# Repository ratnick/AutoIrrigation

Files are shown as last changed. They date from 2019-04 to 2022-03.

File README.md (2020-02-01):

*AUTONOMOUS CLOUD BASED IRRIGATION SYSTEM*

Pitch
=====

Autonomous watering system based on Arduino WEMOS D1 mini, controlled via
Android app through Firebase cloud. PCB design. Case designed and 3D printed.
Key features: Wifi multi-hotspot, Timed Deep sleep / wake-up, persistent memory
in sync with cloud, multiplexing of analogue inputs, Secure Cloud communication.
Updated to also support an MQ-7 CO monitor (https://www.instructables.com/id/Arduino-CO-Monitor-Using-MQ-7-Sensor/).

Table of contents
=================

[1 Pitch 1](#_Toc28007739)

[2 Table of contents 1](#table-of-contents)

[3 Purpose & Description 1](#purpose-description)

[4 Overall Design drivers 1](#overall-design-drivers)

[5 What you will need to get going…and done.
1](#what-you-will-need-to-get-goingand-done.)

[6 System overview 1](#system-overview)

[7 Hardware & PCB 1](#hardware-pcb)

[8 Data flow & global data structure 1](#data-flow-global-data-structure)

[9 Google Firebase Cloud 1](#google-firebase-cloud)

[10 Arduino control software 1](#arduino-control-software)

[11 Android App 1](#android-app)

[12 Cross-platform: Adding new fields in database
1](#cross-platform-adding-new-fields-in-database)

[13 3D printed case 1](#d-printed-case)

[14 Physical Water supply 1](#physical-water-supply)

[15 Connecting it all 1](#connecting-it-all)

[16 Daily use, installation, tuning 1](#daily-use-installation-tuning)

[17 Appendix A - Hardware & PCB version 6.0 - not tested
1](#appendix-a---hardware-pcb-version-6.0---not-tested)

[18 Log History 1](#log-history)

Purpose & Description
=====================

Key use case: I wanted to have an autonomous watering system for outdoor
watering on a city terrasse with the following main requirements:

-   Easy installation:

    -   No wires or cabling

    -   A low-pressure thin water tube to each water station

-   Easy use

    -   No maintenance or battery exchange

    -   Monitoring and control from app

    -   Can run autonomously for at least 3 weeks (during a holiday)

-   Easy scale

    -   Low price per unit

    -   Easy assembly

    -   Reproducible

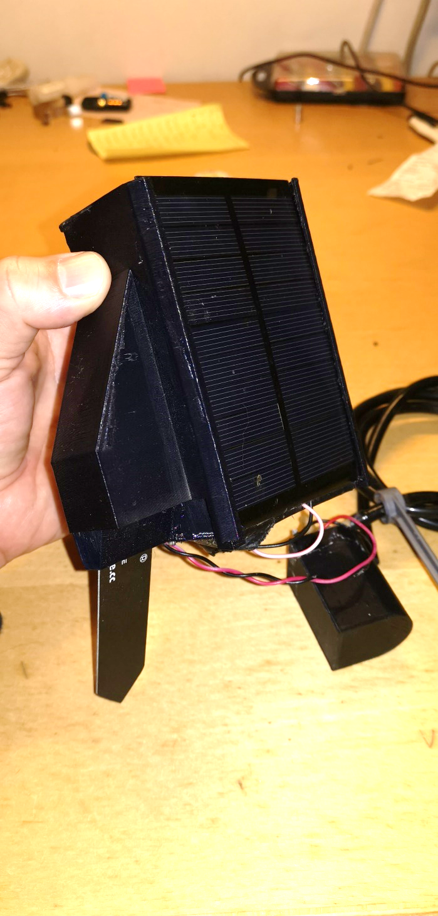
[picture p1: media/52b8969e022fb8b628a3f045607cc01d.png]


Figur 1. The finished unit. Ready to plug into the soil.

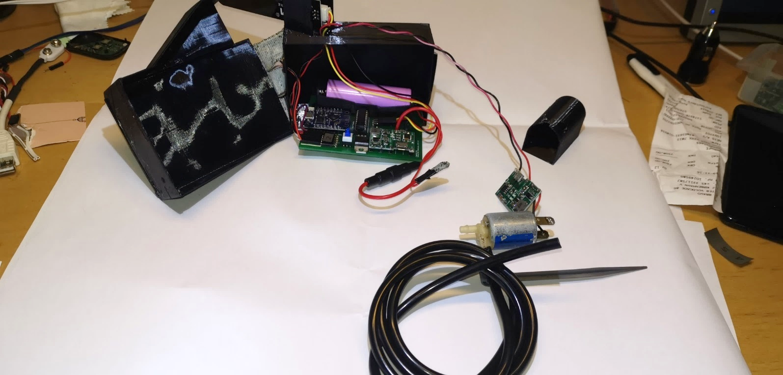
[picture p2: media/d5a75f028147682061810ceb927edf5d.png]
A close up of a piece of paper Description automatically generated


Figur . Same unit - disassembled

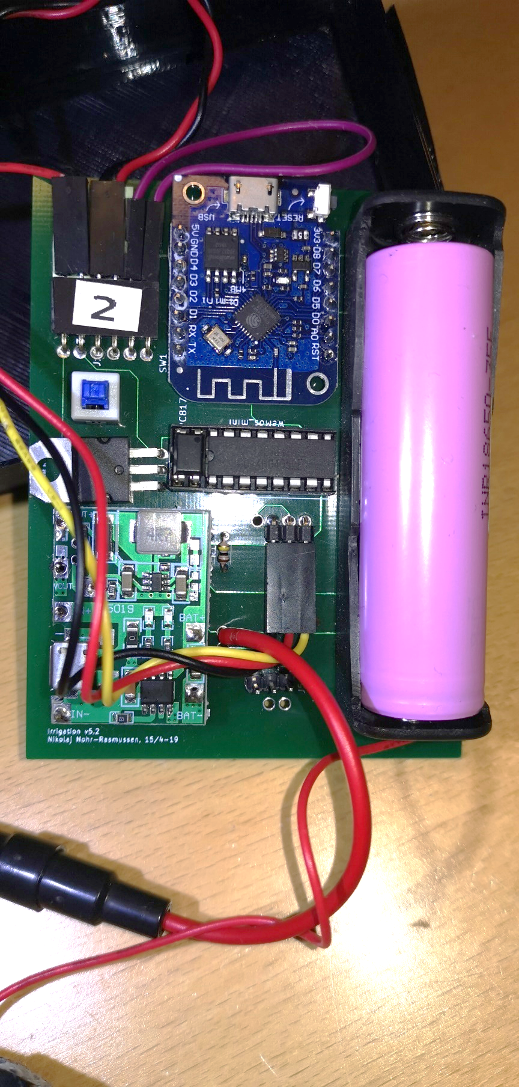
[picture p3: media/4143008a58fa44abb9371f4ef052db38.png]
A circuit board Description automatically generated


Figur 3. Close-up of the PCB

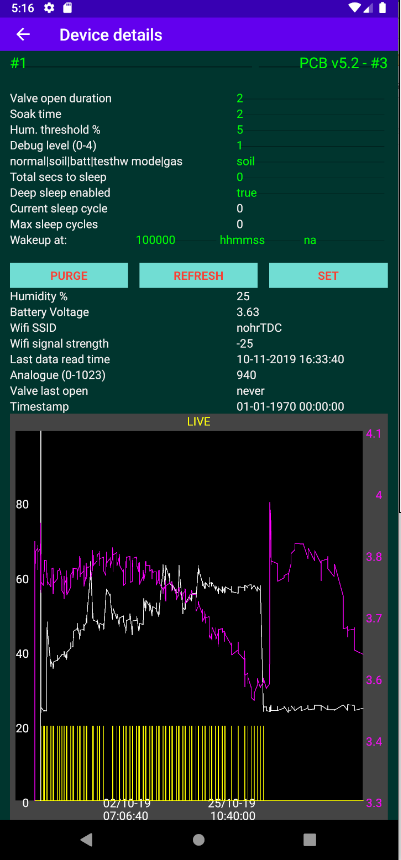
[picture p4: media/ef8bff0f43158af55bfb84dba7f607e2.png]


Figur . The Android app

Overall Design drivers
======================

Based on the key use case, the following was decided up front as system
components:

-   Power supply: Solar panel to power a Li-Ion battery cell.

-   Low water pressure to enable

    -   Thin water hoses (prettier, easy installation, less risk of high water
        spillage if hose breaks).

    -   Solenoid valve with low power consumption.

-   Arduino WeMos D1 Mini

    -   Wifi enabled

    -   Low power

    -   Just enough I/O

    -   Cheap

    -   Small

    -   Large community knowledge

    -   Had already experience with these

-   Cloud based + App

    -   No need for device to be constant online (saves power, gives autonomy)

    -   Collect of telemetry when system online

    -   Enables monitoring and control of device (via app) via internet without
        device being online (commands stored in Cloud)

-   Own 3D printed case

    -   Smallest and cheapest solution…and most fun.

-   Android app

    -   I have an Android phone + tablet

    -   Probably easiest to integrate with a Google Cloud

What you will need to get going…and done.
=========================================

Just to give an indication of the knowledge needed: I am electronics engineer
from 91, and have not been coding professionally since 2000. Besides what I did
on my study, I have never made electronic circuits, no cloud coding, no 3D
modelling, no Android. Except the actual programming, I learned it all through
this and a couple of other projects. So it is not really that advanced - just
get going.

Apart from that, you will need:

-   Some hardware - but not a lot:

    -   Electronics hardware, mainly WeMos D1 mini, a solar panel, and a few
        other components. Details found below.

    -   Water pressure reduction + water hose. Details found below.

-   3D printer + filament. Details below.

-   Soldering tools. Advanced tools not needed.

-   Multimeter is always good.

-   Total cost is less than 15USD per unit, depending on who your “hardware
    pusher is. I am using Aliexpress.

-   Knowledge of

    -   Visual Studio + how to set it up andwork around problems in confurations
        etc.

    -   How to code for Arduino. Of course this works, but you may want to
        modify.

    -   Android SDK + coding in Android.

    -   Autodesk Fusion 360 for 3D models (well - you only need this if you want
        to modify the models).

    -   Google Firebase - step-by-step tutorial included, but again. You
        probably do not want just to clone.

    -   KiCAD knowledge is fine. I started from scratch, and it is fairly
        simple.

    -   Git. Everything is stored on GITHub.

In brieft, you should (details in each section):

1.  Purchase all material.

2.  Download all code, 3D models, documentation and more from GITHub. On top of
    the code, Ive uploaded real source of e.g. the 3D files (and not just the
    printable files), and all the relevant KiCAD files.  
    At least - that was my intent. If something is missing, let me know.

3.  Install the needed tools. You want to find out up front, if there are
    problems here.

4.  Get the PCB ordered - there is some delivery time on this. Gerber files and
    link included (along with source files).

5.  See if everything compiles and installs.

6.  3D print the case. STL files included (along with source files).

7.  Create the firebase account.

8.  When hardware is received, try to install the Arduino/WEMOS software on the
    bare D1 mini. It should at least start and connect to your wifi.

9.  Create and run the Android app. It is actually not needed to test, except if
    you want to delete logs and telemetry. It is also the only way to get a
    graph of the data.

10. When PCB is received, mount all the components.

11. Install the “golden water pressure reducer.

12. Install the water hoses, turn on the water and enjoy a beer.

System overview
===============

Figur . System overview

Hardware & PCB
==============

Tools
-----

1.  All hardware and PCB is designed using KiCAD. Files are found in the GIT
    file.

**Project file: “irrigation v5.2.pro**

NOTE: At the time of writing, I have made a version 6.0 which has not yet been
PCB printed and tested. That can be found in appendix.

Version 5.2 has been in “production for one summer and works fine. Version 6.0
is optimizing the power conversions, which was a bit cumbersome in 5.2. There
are no changes affecting software.

Overview
--------

Figur . Hardware overview.

1.  The hardware modules are all on same PCB, except:

2.  Solar panel

3.  Soil moisture probe

4.  The valve and valve driver (which is a 5V =\> 12V converter). Valve + driver
    has it is own 3D printed case to facilitate that it is stuck in the soil a
    bit away from the probe.

5.  The Lithium battery and the solar panel are both attached to the charge
    unit, which then makes sure to charge the battery whenever possible +
    provides 5V output power for the device.

Components
----------

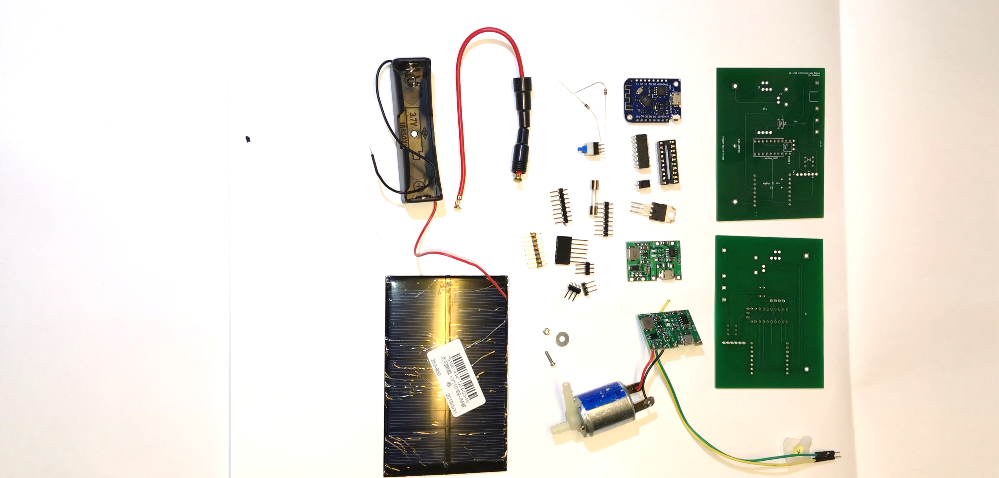
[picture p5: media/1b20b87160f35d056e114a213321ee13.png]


Figur 7. All components. (only 1 PCB is used). (soil sensor missing)

File: irrigation v5.3.html (edited)

| Ref | Qnty | Value | Part | Link | Description |
|---|---|---|---|---|---|
| J1 | 1 | Sol | Connector:Conn_01x02_Female | \~ | Generic connector, single row, 01x02, script generated |
| J2 | 1 | Soil sensor  | Connector:Conn_01x03_Female | \~ | Generic connector, single row, 01x03, script generated |
| J3 | 1 | Valve | Connector:Conn_01x02_Female | \~ | Generic connector, single row, 01x02, script generated |
| J4 | 1 | Batt | Connector:Conn_01x02_Female | \~ | Generic connector, single row, 01x02, script generated |
| J5 | 1 | Spare conn.  | Connector:Conn_01x03_Female | \~ | Generic connector, single row, 01x03, script generated |
| Opto1 | 1 | PC817 | Isolator:PC817 | <https://www.aliexpress.com/item/Free-Shipping-20pcs-lot-PC817C-PC817-EL817-EL817C-DIP-4-817-transistor-output-optocoupler/2040307423.html> | DC Optocoupler, Vce 35V, CTR 50-300%, DIP4 |
| Q1 | 1 | TIP120 | Transistor_BJT:TIP120 | <https://www.aliexpress.com/item/10PCS-TIP102-TIP120-TIP122-TIP127-TIP142-TIP147-LM317T-IRF3205-Transistor-TIP142T-TIP147T/32868103655.html> | 5A Ic, 60V Vce, Silicon Darlington Power NPN Transistor, TO-220 |
| R1 | 1 | 100k | Device:R | \~ | Resistor |
| R2 | 1 | 5k | Device:R | \~ | Resistor |
| Not shown | 1 | SOIL_SENSOR  | SOIL_SENSOR | <https://www.aliexpress.com/item/32832538686.html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,searchweb201602_3,searchweb201603_53> | Capacitive soil moisture sensor |
| SW1 | 1 | ON/OFF | Switch:SW_SPST | | Single Pole Single Throw (SPST) switch |
| SW2 | 1 | flash | Switch:SW_Push_Open | | Push button switch, push-to-open, generic, two pins |
| U2 | 1 | WeMos_mini | wemos_mini:WeMos_mini | <https://www.aliexpress.com/item/ESP8266-ESP-12-ESP-12F-CH340G-CH340-V2-USB-WeMos-D1-Mini-WIFI-Development-Board-D1/32633763949.html> | WeMos D1 mini |
| U4 | 2 | J5019 | NNR-lib:J5019 | <https://www.aliexpress.com/item/Lithium-Li-ion-18650-3-7V-4-2V-Battery-Charger-Board-DC-DC-Step-Up-Boost/32901921699.html> | J5019 Lithium Li-ion 18650 3.7V 4.2V Battery Charger Board DC-DC Step Up Boost Module |
| U5 | 1 | CD4052B | Analog_Switch:CD4052B | <https://www.aliexpress.com/item/Free-shippin-10pcs-lot-CD74HC4052E-CD74HC4052-74HC4052-DIP16-Switches-new-original/32549841035.html> | CMOS double 4-channel analog multiplexer/demultiplexer, TSSOP-16/DIP-16/SOIC-16 |
| bat_18650 | 1 | Battery_Cell | Device:Battery_Cell | 18650 battery cell | |
| Not shown | 1 | valve | 12V Normally closed solenoid valve | <https://www.aliexpress.com/item/32850727204.html> | |
| Not shown | 1 | Solar panel  | | | |

Schematics
----------

File: irrigation v5.3.sch

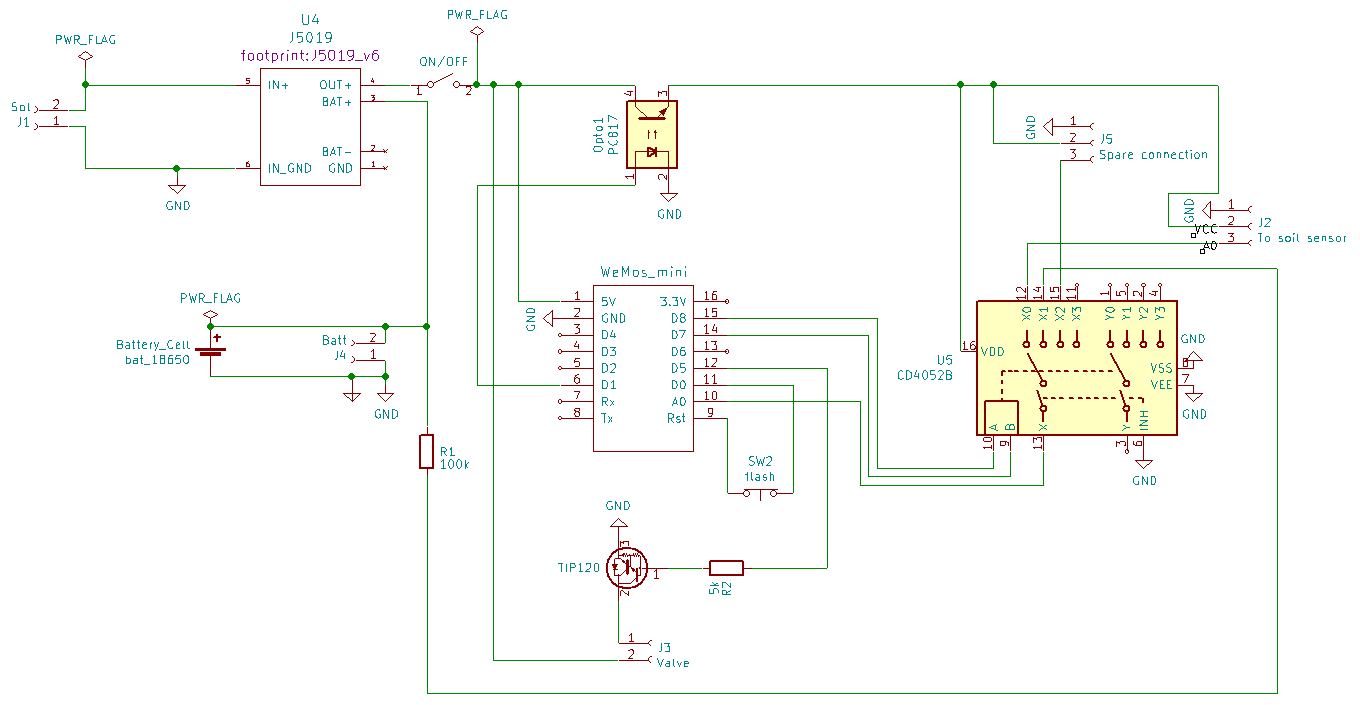
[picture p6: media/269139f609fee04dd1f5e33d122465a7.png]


Figur . Schematics.

PCB layout
----------

Supplier: <https://firstpcb.com/>

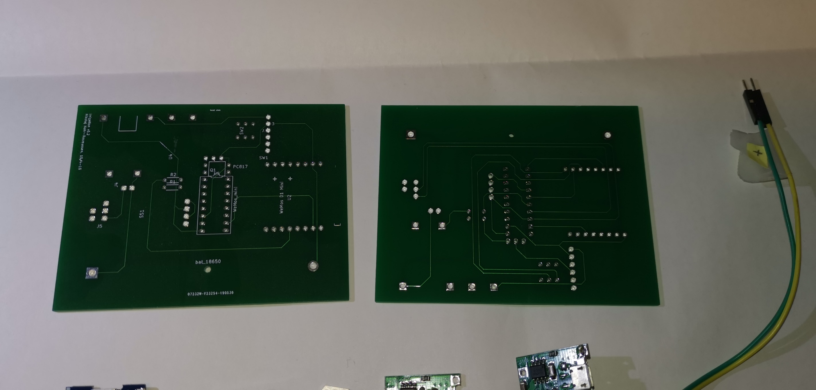
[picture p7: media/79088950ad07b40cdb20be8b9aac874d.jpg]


File: irrigation v5.3.kicad_pcb

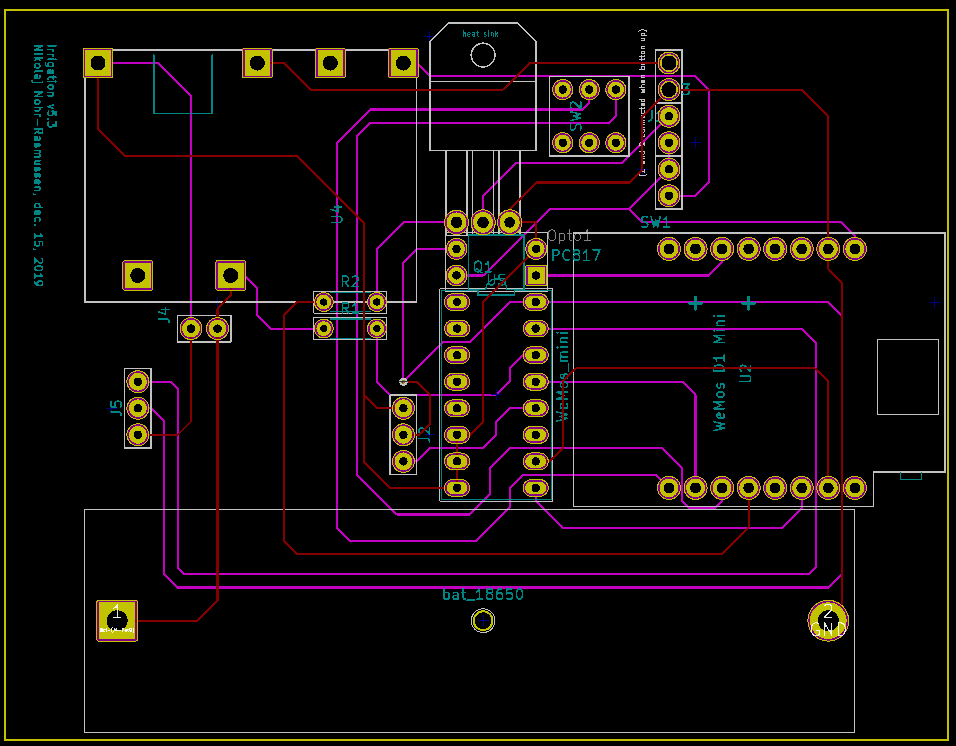
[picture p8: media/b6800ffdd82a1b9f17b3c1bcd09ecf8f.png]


Figur . PCB layout.

Considerations & Notes
----------------------

If this should be made significantly smaller, the way is first to get rid of all
the boards, and use only the components. This is however a “fair amount of work,
and deemed not worth the effort.

Export PCB for print
--------------------

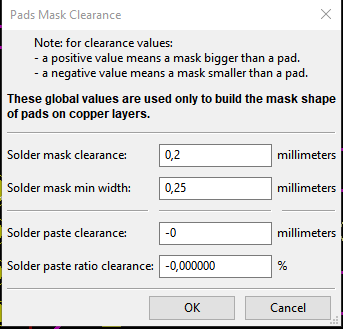
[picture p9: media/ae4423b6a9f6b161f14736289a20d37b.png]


### Export to Gerber files

Result should be the following set of files:

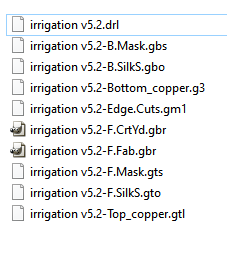
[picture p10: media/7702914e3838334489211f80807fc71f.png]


File -\> Plot

Note: It may not be the exact correct values set below.

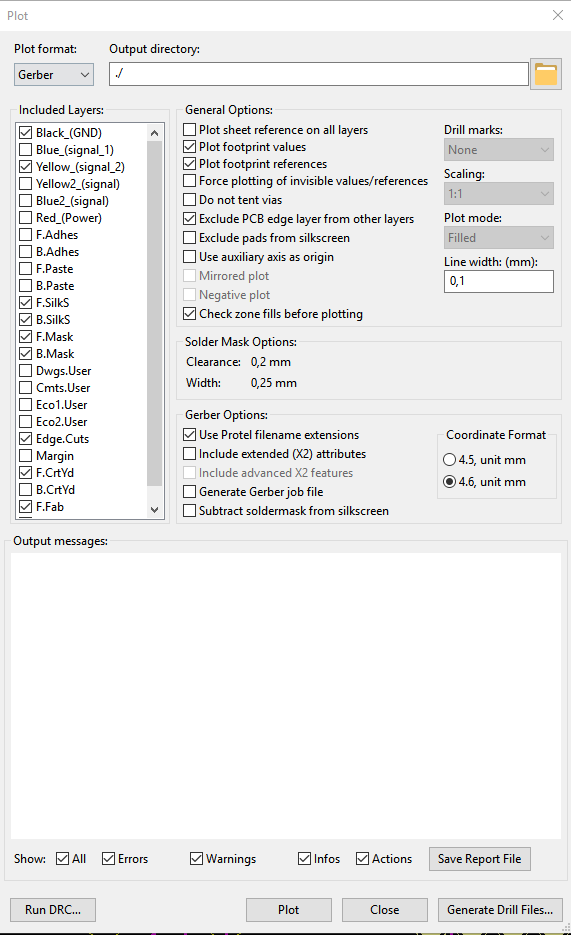
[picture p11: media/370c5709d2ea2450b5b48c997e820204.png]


Drill holes:

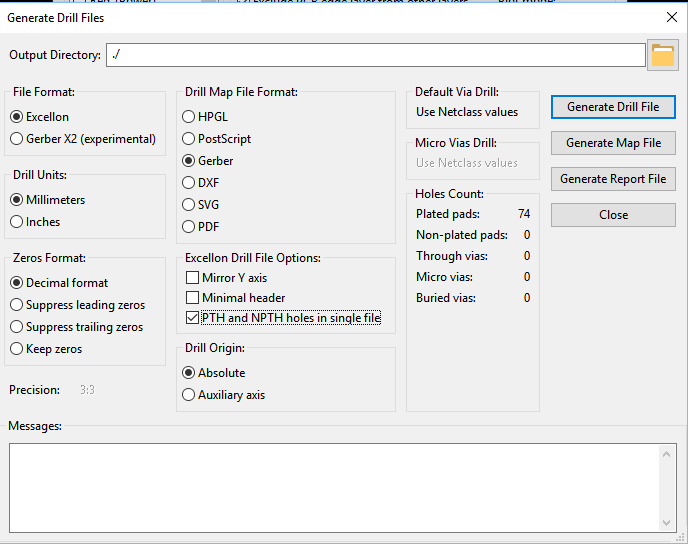
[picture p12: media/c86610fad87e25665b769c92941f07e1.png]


Data flow & global data structure
=================================

Note: Firebase is a JSON database, meaning that it is NOT structured in tables
(like a relational database is).

System Data Flow
----------------

Data structure
--------------

| Table | Field name (in Arduino code) | JSON name (Firebase and Android) | Type | Notes / usage |
|---|---|---|---|---|
| **Irrdevice** | | | | **(one child per device)** |
| **metadata** | | | | **(Semi-static configuration, can be updated runtime)** |
| | macAddr | mac | String  | (not updatable, used as unique device key) |
| | location | loc | String  | Physical location, e.g. “ved gasbrænderen |
| | deviceID | device | String  | Hardcoded to device model identifier, PCB version etc |
| | sensorType | sensor type | String  | What sensor type is used (for future scaling to other kinds of sensors) |
| | hardware | hw | String  | Which hardware is used |
| | softwareVersion | sw | String  | Software name and compile time |
| **state** | | | | **(updated by device)** |
| | SSID | SSID | String  | Current hotspot |
| | runOnce | runOnce | boolean | Used for debugging and testing |
| | timestamp | timestamp | long | ms since 1970. |
| | | | | Assigned on Firebase server side |
| | sleepCurCycle | slpCurCyc | int | Current sleep cycle. Between zero and sleepMaxCycles |
| | sleepSecondsToSleep | slpDura | Int | Seconds See below |
| | sleepMaxCycles | slpMxCyc | Int | See below |
| **settings** | | | | **(can be set runtime by both device and user)** |
| | UserUpdate | Updated | boolean | Set to true by app or user if user updates any value. Set to false by device when device reads the values. |
| | runMode | runMode | String  | Soil\|water\|gas\|sensor\|batt\|testhw The device can run in different modes. For normal autonomous watering, use “soil |
| | valveOpenDuration | vlvOpen | Int | Seconds the valve is open (if soil is too dry) |
| | soakTime | vlvSoak | Int | Seconds until soil humidity is measured after watering. |
| | humLimit | humLim | int | Percentage If humidity \< humlimit, watering will be performed. |
| | mainLoopDelay | loopSec | Int | Seconds to wait between the loop cycles within a single power cycle. The device is awake during this waiting time, so it should not be too long. |
| | debugLevel | db | int | 0: only fatal errors are logged to the Firebase log 1-4: more and more logs. |
| | sleepEnabled | slpEnabl | boolean | Sleep control parameter. |
| | totalSecondsToSleep | totSlp | int | Sleep control parameter. Total seconds for a sleep cycle. During runtime it is converted to sleepSecondsToSleep and sleepMaxCycles as: sleepMaxCycles = \# of cycles sleeping at max_sleep_duration (hardware number) sleepSecondsToSleep = remainder (last sleep cycles has this duration). |
| | wakeupTime[0..3] | wakeTime0 wakeTime1 wakeTime2 wakeTime3 | String  | Sleep control parameter. HHMMSS 0/1/2 used to set 3 different wake up times per day. 3 is used internally by the device and should not be altered. |
| | pauseWakeTime | pauseTime | String  | Sleep control parameter. HHMMSS NOTE: This is not used by the device. Left-over. |
| **telemetry\_** | | | | **(last set of values received from device)** |
| **current** | | | | |
| | Vcc | Vcc | float | Measured battery voltage (provided measurement mode is “battery voltage ) |
| | humidity | Hum | float | Measured humidity (provided measurement mode is “humidity ) |
| | lastAnalogueReading | lastAnalog | int | Voltage Raw reading (0-1023) |
| | lastOpenTimestamp | lastOpen | string  | Time when the valve was opened the last time (readable format) |
| | timestamp | timestamp | long | ms since 1970. |
| | | | | Assigned on Firebase server side |
| | valveState | vlvState | int | 0: valve closed, 1: valve open |
| | wifi | Wifi | int | Wifi signal strength in dB |
| **telemetry** | | | | **all values received from device. One entry per timestamp** |
| | Same as telemetry_current | | | |
| **log** | | | | **Real time log (controlled by debugLevel)** |
| | time | ts | | |
| | text | txt | | |

Considerations & Notes
----------------------

Google Firebase Cloud
=====================

We use a **Google Firebase Realtime database** as cloud.

Configuration
-------------

1.  <https://console.firebase.google.com/>

2.  Sign up, if needed.

3.  Create a project: Create project

    1.  Name: irrigation

        1.  Note that this name is used in noth Arduino (FIREBASE_HOST)

        2.  Android code (FB_PROJECT_ID) + in app/google-services.json

    2.  ID: irrigation-XXXXXXX

4.  Activate the free trial, if needed



1.  Select Develop =\> Database

2.  Choose to create a new Realtime Database (NOT a Cloud Firestore). Start in
    test mode, but be aware to change later.

    1.  Auth tokens (Database secrets)

Go to Project overview -\> Settings -\> Service accounts

Show and Copy the “secret and insert into Arduino code (typically called
FIREBASE_AUTH)

-   Used in Arduino code in autoirrigation.ino

-   Android code: in app/google-services.json

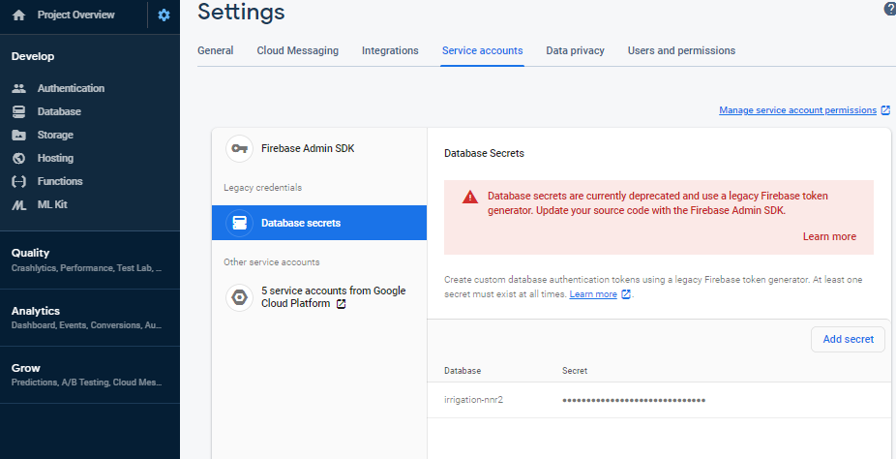
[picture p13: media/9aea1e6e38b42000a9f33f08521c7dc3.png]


Links
-----

<https://github.com/GoogleCloudPlatform/google-cloud-iot-arduino>

<https://console.cloud.google.com/home/dashboard?project=cohesive-photon-227011>

<https://console.cloud.google.com/iot/registries?project=cohesive-photon-227011&folder&organizationId&pli=1>

<https://console.cloud.google.com/iot/registries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>

Arduino control software
========================

Features
--------

The Arduino software has the following features:

-   Wifi handling

    -   The device will look up a number of predefined hotspots and hook up to
        the first with signal strength above a threshold (to save power, we will
        not hook up to a very weak hotspot).

    -   It will remember the last good hotspot, which allows that the device can
        be moved between e.g. the office and the garden.

-   Deep sleep handling using

    -   Timed wakeup (there are 3 timers per day)

    -   Periodic wake-up: set the time until next wake-up

-   Persistent memory handling

    -   Maintains a mirror of the settings in the cloud. When waking, it reads
        setting, if they have been altered by the user. During runtime, some
        settings may be changed and uploaded to the cloud.

    -   Settings only used internally by device, e.g. last used wifi password
        that worked

-   Multiplexing of analogue input signals

    -   The device can control a multiplexer, allowing to read from several
        sensors. The D1 mini only has one analog port.

    -   This feature also controls the power supply to the sensors (so they only
        use power when measuring).

-   Secure Cloud communication.

    -   There are functions to communicate with Firebase, Azure and Google
        Cloud. Each cloud has it is drawbacks and advantages. This is compile
        time controlled.

Software Components
-------------------

-   Globals (globals, firebasemodel)

    -   Global types and structures

    -   Global names and constants

-   Configuration and main control (autoirrigation.ino)

    -   Compile time configuration

    -   Runtime configuration

    -   Debug configuration

    -   Authentication info

    -   Operating modes (test modes)

    -   Type of device (I am also developing a CO gas sensor; not yet finished)

    -   All communication to cloud (note: there is working software for using
        both Azure and Google Cloud)

-   Power & Sleep (deepsleephandler)

    -   Deep Sleep management

-   Persistent storage (persistentmemory)

    -   Control of the internal persistent memory in the D1. Essentially
        maintaining a mirror of the settings in Firebase.

-   Sensors (analogmux, sensorhandler, soilhumiditysensor, watersensor,
    voltmeter, gassensor)

    -   Multiplexer control

    -   Configuration (different sensors can be used in different ways)

    -   initialization

    -   monitoring

-   Actuators (watervalve, LEDhandler)

    -   Configuration & link to sensors

    -   Initialization

    -   Controlling

-   Wifi mgt (wifi_nnr, wifihandler)

    -   Initialization

    -   connectivity

-   Cloud comm (incl in autoirrigation.ino)

    -   connection

    -   reporting

Tools & setup
-------------

-   Visual Studio Community 2019

-   vMicro extension

-   Create the file wifipasswords.h as described in wifi_nnr.ino. You cant
    compile without it.

-   Install my homemade libraries (also found on my GITHub).

-   Install all needed arduino libraries. Just continue installing until you run
    out of compilation errors 😊

### vMicro extension setup

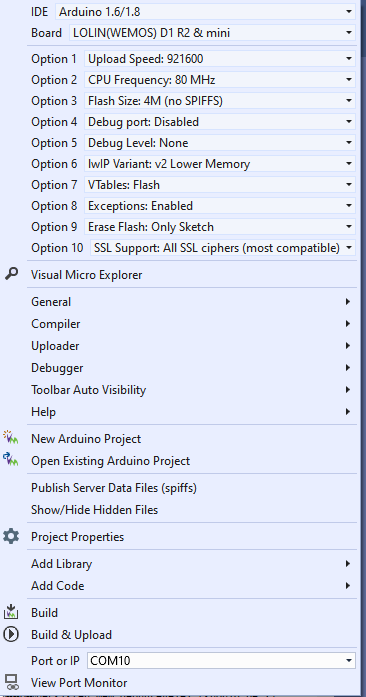
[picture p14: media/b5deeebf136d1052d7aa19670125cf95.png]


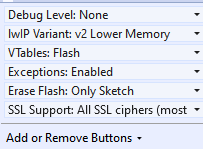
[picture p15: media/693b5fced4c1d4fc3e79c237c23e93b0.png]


### Uploading to board - and problems/tips

Note that when uploading there are two things that can tease a bit:

-   Remember to push the small “flash button before flashing. “Unpush the button
    when flashed - otherwise the board will not reset.get if you forget is
    something like “The uploader process failed .

-   If the board is in a long series of sleeps, it will wake up, and immediately
    go back to sleep each time it is reset - until the sleep counter reach it is
    target (zero). You can follow that in the serial output window. Disable this
    by disabling UseSleepMode.

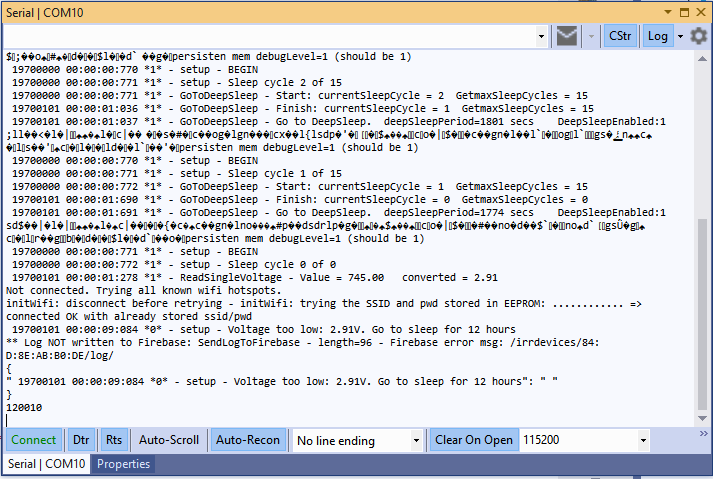
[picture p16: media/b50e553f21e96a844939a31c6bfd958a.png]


Figure 1. The sleep feature may tease when debugging.

-   If the battery voltage is too low, the board will enter sleep immediately.
    This may provoke a crash dump somehow. Not sure why, but it looks like this.
    If it happens - charge the battery.

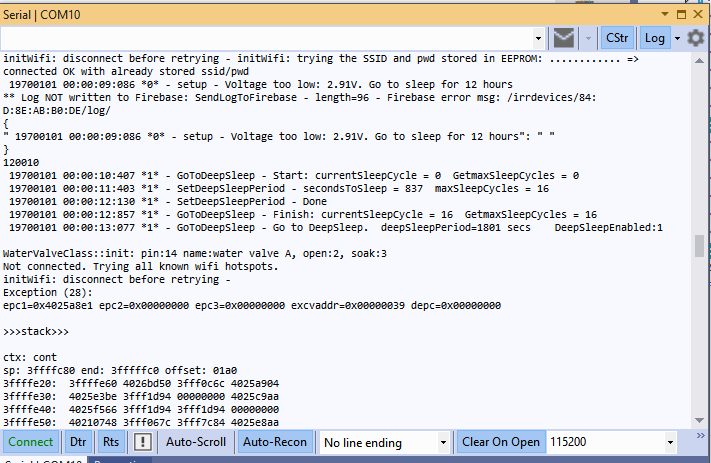
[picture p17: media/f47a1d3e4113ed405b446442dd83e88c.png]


Figure 2. Message you get if battery is flat.

Future features:
----------------

-   OTA update. That would really be nice - in particular because the devices
    are placed outdoor in soil.

Android App
===========

I may use wrong terminology here - I am not very familiar with Android. But the
simple app works 😊

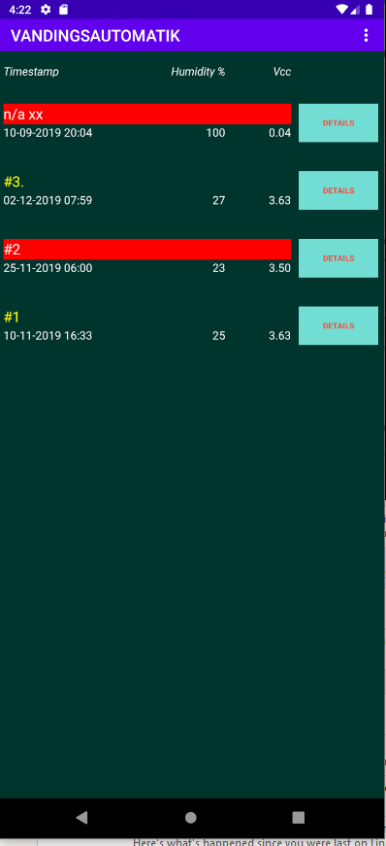
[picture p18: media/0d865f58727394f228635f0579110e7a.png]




Features
--------

-   Hooks up to Firebase and reads + writes data

-   Presents a graph of the data

Overview
--------

-   Main layout:

    -   List of all devices in Firebase with most important data + color code
        for status.

-   Single device layout

    -   Zoom to all relevant settings (yellow) and telemetry of a single device.

    -   Options for purging both telemetry and log data (if there is a lot of
        data, I have not found a way to purge from the WEB interface to
        Firebase).

-   Background service

    -   Maintaining the interface to Firebase + the data

configuration
-------------

Get the google-services.json configuration file from:
<https://support.google.com/firebase/answer/7015592?hl=en>

Tools
-----

-   Android Studio used

Cross-platform: Adding new fields in database
=============================================

Arduino 
--------

Data structure is defined in source code files:

-   Globals.h

-   Persistentmemory.cpp

-   AutoIrrigation.ino

    -   Function CreateTelemetryJson() defines the data transmitted.

-   WaterValve.h

-   WaterSensor.h

Android
-------

-   Source files defining the data structure is under com.vanding.datamodel/

-   FirebaseObject.java encapsulate this data

-   res/layout/content_main.xml and content_single_device.xml contains the
    visual implementation.

3D printed case
===============

Order of design
---------------

1.  Model each hardware component. Placed in separate proejcts.

2.  Import needed

3.  Place them physically as wished

4.  Create base floor. Project spefici markers from the needed components -
    nothing else.

Main components
---------------

F3d files: 3D models of hardware components. This makes it way easier to try out
different layouts.

F3z files: Design of the casing for the irrigation unit. These are importing the
hardware models.

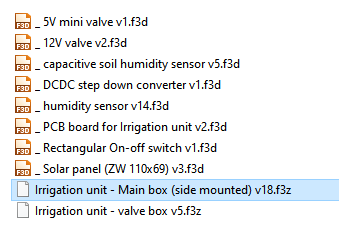
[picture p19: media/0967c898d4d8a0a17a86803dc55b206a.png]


### Main Box for PCB

File: Irrigation unit - Main box (side mounted)

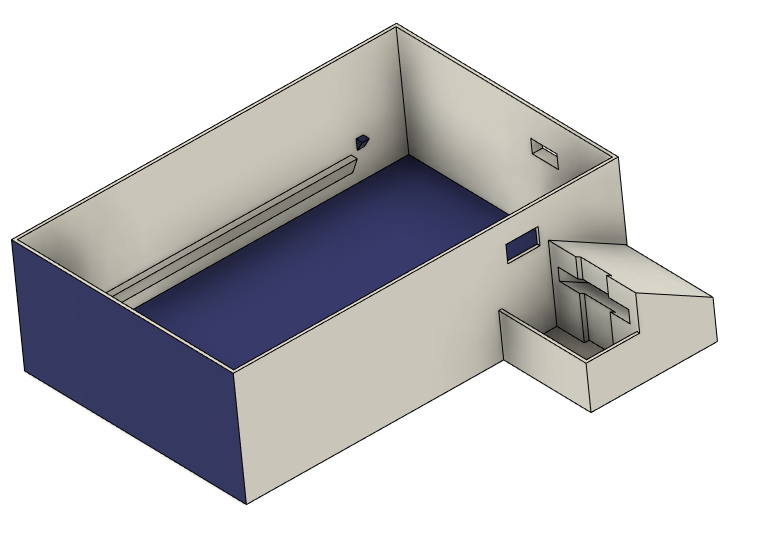
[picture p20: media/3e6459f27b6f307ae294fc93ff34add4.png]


Figur . Main box

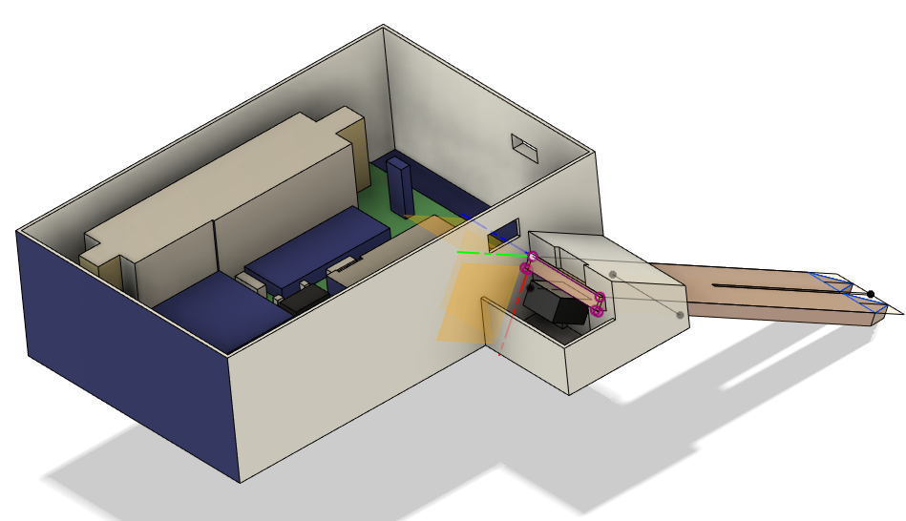
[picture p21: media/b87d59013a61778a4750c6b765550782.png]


Figur 11. Main box with model of PCB and soil sensor.

### Top box with solar panel

File: Irrigation unit - Main box (side mounted)

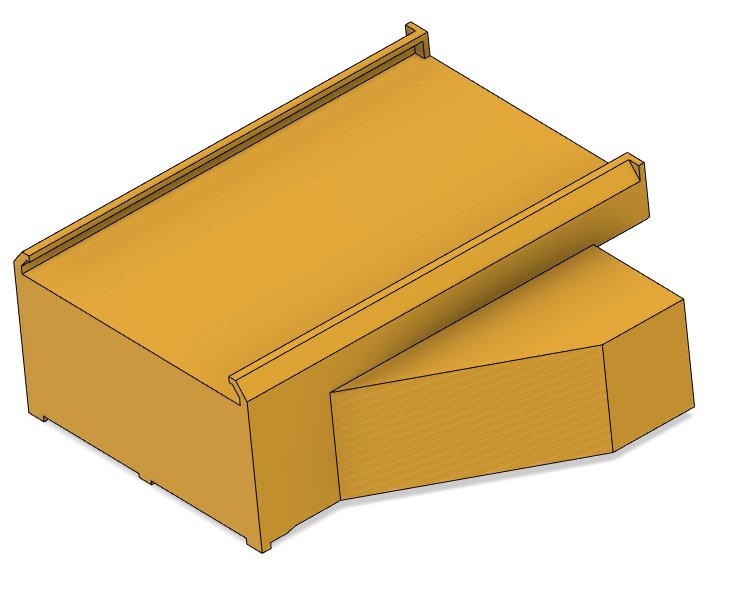
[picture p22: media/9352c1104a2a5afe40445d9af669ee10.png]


Figur 12. Ceiling to main box

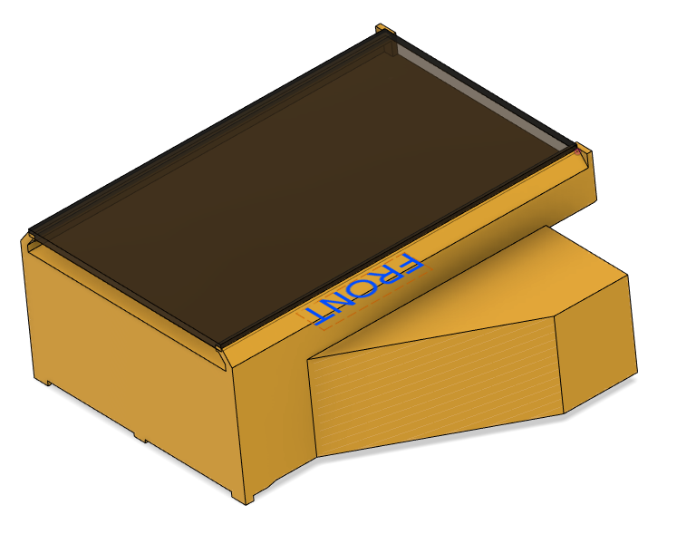
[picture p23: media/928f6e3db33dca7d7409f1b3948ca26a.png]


Figur . ...with solar panel

### Box for valve and valve driver

File: Irrigation unit - valve box

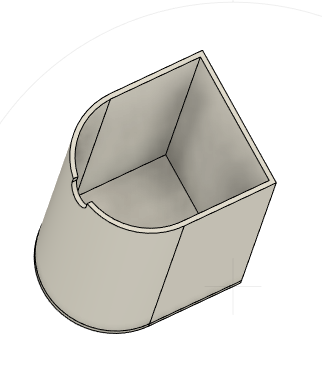
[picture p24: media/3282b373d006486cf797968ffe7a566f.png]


Figur 14. Box for valve and valve driver - seen from the bottom.

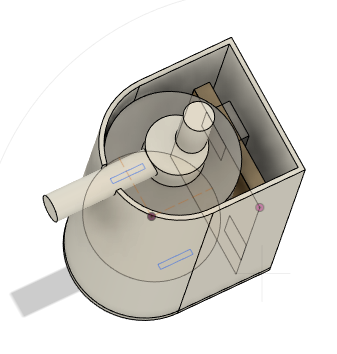
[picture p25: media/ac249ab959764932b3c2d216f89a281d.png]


Figur ...with components inside

Considerations and notes
------------------------

The principles has been to make it rain resistant by using the fact that “water
do not run upwards 😊 . So it is not water or dust tight, but it can withstand
heavy rain, as long as the device is properly put in the ground.

Tools
-----

-   AutoDesks Fusion360

-   XYZWare Da Vinci Mini w 3D printer

Physical Water supply
=====================

A regular water outlet produce way too much pressure, so reducing the pressure
is essential. It is the basis for

-   reducing risk of water spill in case of malfunctions somewhere

-   reducing power consumption. A higher pressure requires a stronger valve,
    requiring much more power.

-   Having a visually lighter installation, i.e. thinner hoses.

Hardware
--------

### 4/6 mm (inner/outer diameter) flexible water hose.

(link may come later)

### Adjustable water pressure reducer

<https://www.aliexpress.com/item/DN15-Adjustable-Brass-Water-Pressure-Reducing-Regulator-Valve-Internal-and-outer-thread-PN-1-6-and/32964829770.html>

DN15 Adjustable Brass Water Pressure Reducing Regulator Valve Internal and outer
thread PN 1.6 and Pressure Gauge.

-   Material: Brass

-   Connector Size: DN15(G1/2 )

-   Connection Type: Internal /outer Thread

-   Package Contents:

-   1 x Water Pressure Reducing Valve+Wrench+raw material belt

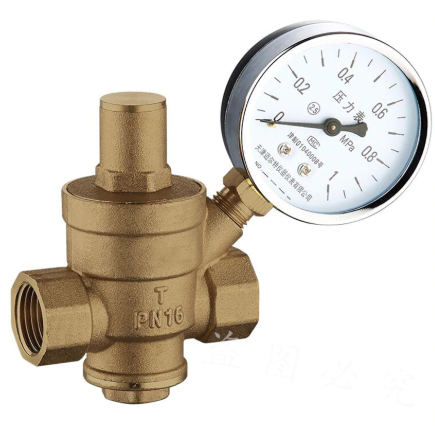
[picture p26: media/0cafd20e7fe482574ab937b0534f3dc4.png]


Adjustment
----------

From my memory, water pressure is around 0,1 bar. If it is too high, the valve
will not operate. If too low then it takes too long to water =\> higher power
consumption. An open valve uses \~10W (12V, 1A).

Connecting it all
=================

When done, there are a few pieces that need to be put together.

The main pieces are here:

Daily use, installation, tuning
===============================

Installation 
-------------

The hard work pays off:

-   Install the water tubes

-   Install each device. Give each device a good name - and maybe a sticker on
    the outside, so you can recognize it visually.

-   Make sure the wifi works, check the strength.

-   Check via the app

Appendix A - Hardware & PCB version 6.0 - not tested
====================================================

Version 6.0 is optimizing the power conversions, which was a bit cumbersome in
5.2. There are no changes affecting software.

Components
----------

File: irrigation v6.0.html

**Component Count:**16

| Ref | Qnty | Value | Part | Description | Vendor |
|---|---|---|---|---|---|
| J1 | 1 | Connector to Solar panel | Connector:Conn_01x02_Female | Generic connector, single row, 01x02, script generated (kicad-library-utils/schlib/autogen/connector/) | |
| J2 | 1 | Connector to Batt | Connector:Conn_01x02_Female | Generic connector, single row, 01x02, script generated (kicad-library-utils/schlib/autogen/connector/) | |
| J3, J4 | 2 | Connector to Valve | Connector:Conn_01x02_Female | Generic connector, single row, 01x02, script generated (kicad-library-utils/schlib/autogen/connector/) | |
| J5 | 1 | Connector to Capacitive soil sensor | Connector:Conn_01x03_Female | Generic connector, single row, 01x03, script generated (kicad-library-utils/schlib/autogen/connector/) | |
| L1 | 1 | 12V Valve | Device:Electromagnetic_Actor | Electromagnetic actor | |
| Opto1 | 1 | PC817 | Isolator:PC817 | DC Optocoupler, Vce 35V, CTR 50-300%, DIP4 | <https://www.aliexpress.com/item/Free-Shipping-20pcs-lot-PC817C-PC817-EL817-EL817C-DIP-4-817-transistor-output-optocoupler/2040307423.html> |
| Q1 | 1 | TIP120 | Transistor_BJT:TIP120 | 5A Ic, 60V Vce, Silicon Darlington Power NPN Transistor, TO-220 | <https://www.aliexpress.com/item/10PCS-TIP102-TIP120-TIP122-TIP127-TIP142-TIP147-LM317T-IRF3205-Transistor-TIP142T-TIP147T/32868103655.html>  |
| R1 | 1 | 100k | Device:R | Resistor | |
| R2 | 1 | 5k | Device:R | Resistor | |
| SW1 | 1 | flash | Switch:SW_Push_Open | Push button switch, push-to-open, generic, two pins | |
| U1 | 1 | J5019 | NNR-lib:J5019 | J5019 Lithium Li-ion 18650 3.7V 4.2V Battery Charger Board DC-DC Step Up Boost Module | <https://www.aliexpress.com/item/Lithium-Li-ion-18650-3-7V-4-2V-Battery-Charger-Board-DC-DC-Step-Up-Boost/32901921699.html> |
| U2 | 1 | 12-24V to 1.8-12V_DCDC_converter | NNR-lib:12-24V-1.8-12V_DCDC_converter | | <https://www.aliexpress.com/item/Ultra-Small-Size-DC-DC-Step-Down-Power-Supply-Module-3A-Buck-Converter-Adjustable-1-8V/32880983608.html> |
| U3 | 1 | WeMos_mini | wemos_mini:WeMos_mini | WeMos D1 mini R2 | <https://www.aliexpress.com/item/ESP8266-ESP-12-ESP-12F-CH340G-CH340-V2-USB-WeMos-D1-Mini-WIFI-Development-Board-D1/32633763949.html> |
| U4 | 1 | CD4052B | Analog_Switch:CD4052B | CMOS double 4-channel analog multiplexer/demultiplexer, TSSOP-16/DIP-16/SOIC-16 | <https://www.aliexpress.com/item/Free-shippin-10pcs-lot-CD74HC4052E-CD74HC4052-74HC4052-DIP16-Switches-new-original/32549841035.html> |
| bat_1 | 1 | Battery_Cell | Device:Battery_Cell | Single-cell battery type 18650 | |
| SOLAR | 1 | Solar panel | | | <https://www.aliexpress.com/item/ANBES-Solar-Panel-5V-6V-12V-Mini-Solar-System-DIY-For-Battery-Cell-Phone-Chargers-Portable/32848710253.html> |
| Not shown | 1 | valve | 12V Normally closed solenoid valve | | <https://www.aliexpress.com/item/32850727204.html> |

Schematics
----------

File: irrigation v6.0.sch

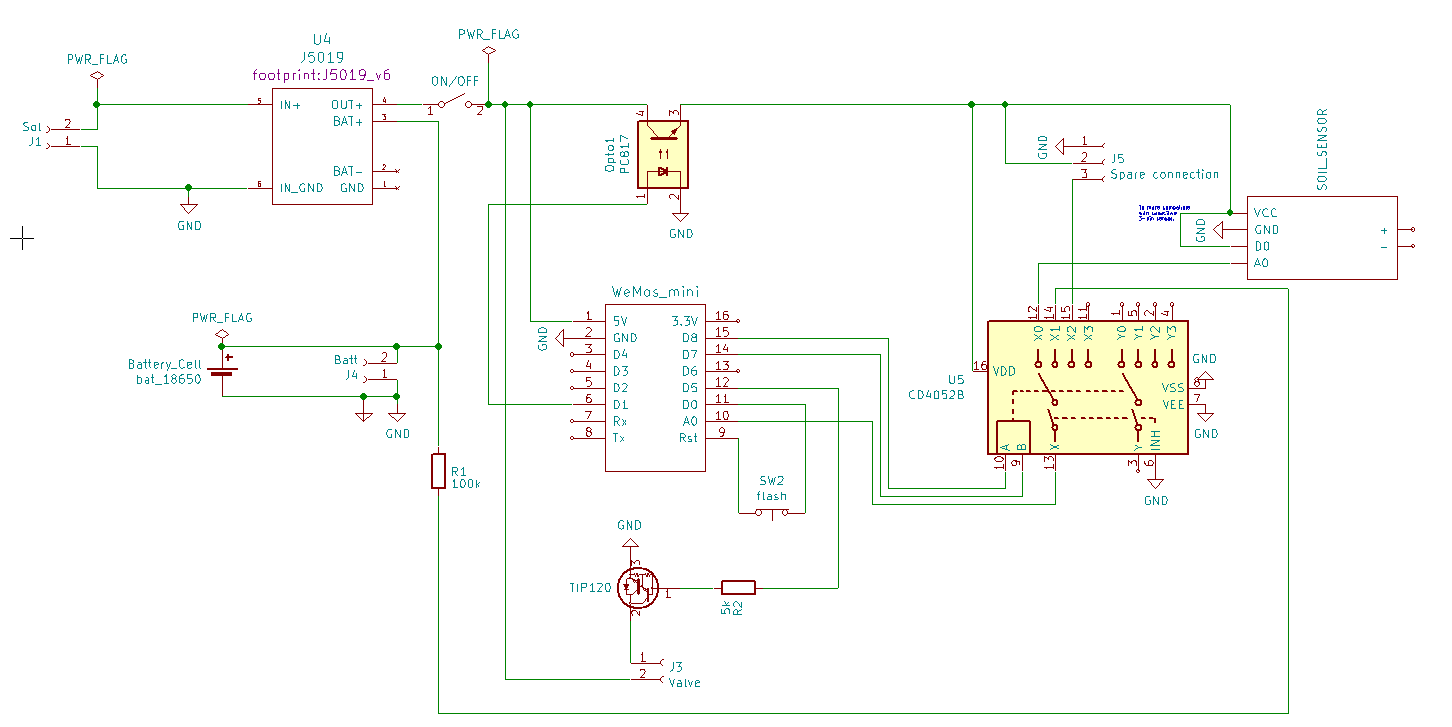
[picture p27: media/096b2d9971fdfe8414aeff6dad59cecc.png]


PCB layout
----------

File: irrigation v6.0.kicad_pcb

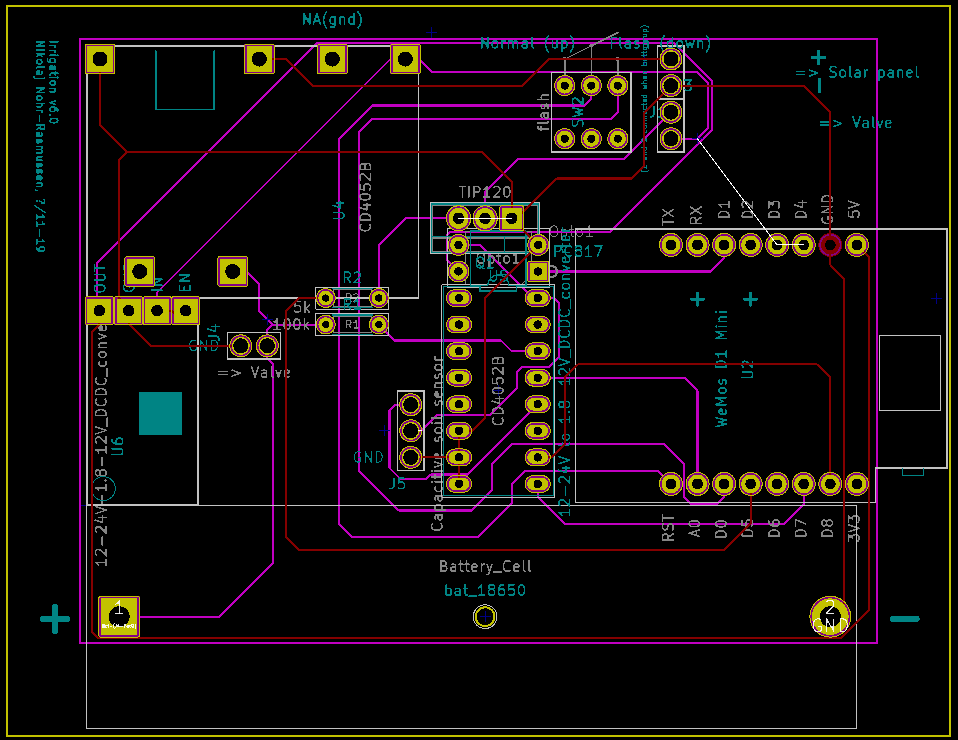
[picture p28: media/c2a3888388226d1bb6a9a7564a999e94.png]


Log History
===========

| Date | Updates | Affected modules |
|---|---|---|
| 15-dec-2019 | Initial public version | all |
| | | |

Save this file as ../README.MD to publish on GitHub with embedded pictures.

Install the plugin <http://www.writage.com/> and export directly from Word.

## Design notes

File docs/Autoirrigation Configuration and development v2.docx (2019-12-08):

# Purpose & Description

Problem: I wanted to have an autonomous watering system for outdoor watering with the following main requirements:

- No wires or cabling
- A low-pressure thin water tube to each water station
- Low price per unit
- No maintenance or battery exchange
- Monitoring and control from app

# System overview

# Hardware & PCB

## 1 Tools

KiCAD has been used.

## 2 Components

## 3 Schematics

## 4 PCB layout

# Data flow & data structure

# Firebase Cloud

# Arduino software

# Android App

# 3D printed case

# Water system

# Daily use, installation, tuning

# Data structure

- JSON database

Table | Field name (in Arduino code) (lower is new name) | NEW JSON name (Firebase and Android) | Type | Notes / usage
Irrdevice | | | | (on child per device)
metadata | | | | (Semi-static configuration, can be updated runtime)
| macAddr | mac | String | (not updatable, used as unique device key)
| location | loc | String | Physical location, e.g. “ved gasbrænderen”
| deviceID | device | String | Free to use
| hardware | hw | String | Which hardware is used
| softwareVersion | sw | String | Software name and compile time
state | | | | (updated by device)
| SSID | SSID | String | Current hotspot
| runOnce | runOnce | boolean | Used for debugging and testing
| timestamp | timestamp | long | ms since 1970. Assigned on Firebase server side
| curSleepCycle sleepCurCycle | slpCurCyc | int | Current sleep cycle. Between zero and sleepMaxCycles
| secsToSleep sleepSecondsToSleep | slpDura | Int | Seconds See below
| maxSlpCycles sleepMaxCycles | slpMxCyc | Int | See below
settings | | | | (can be set runtime by both device and user)
| UserUpdate | Updated | boolean | Set to true by app or user if user updates any value. Set to false by device when device reads the values.
| deepSleepEnabled sleepEnabled | slpEnabl | boolean
| totalSecondsToSleep sleepTotalDuration | totSlp | int | Seconds. Is converted to sleepSecondsToSleep and sleepMaxCycles as: sleepMaxCycles = # of cycles sleeping at max_sleep_duration (hardware number) sleepSecondsToSleep = remainder (last sleep cycles has this duration).
| openDur valveOpenDuration | vlvOpen | Int | Seconds
| soakTime | vlvSoak | Int | Seconds
| humLimit | humLim | Int | Pct humidity to trigger valve opening
| mainLoopDelay | loopSec | Int | Seconds
| mode measurementMode | mode | String | “normal” “tuneSoilsensor” “testhw”
telemetry_ current | | | | (last set of values received from device)
| Vcc | Vcc | float | Measured battery voltage (provided measurement mode is “battery voltage”)
| humidity | Hum | float | Measured humidity (provided measurement mode is “humidity”)
| lastAnalogueReading | lastAnalog | int | Voltage Raw reading (0-1023)
| lastOpenTimestamp | lastOpen | String
| timestamp | timestamp | long | ms since 1970. Assigned on Firebase server side
| valveState | vlvState | int
| wifi | Wifi | int | Wifi signal strength
telemetry | | | | all values received from device. One entry per timestamp
| Equal to Telemetry_Current
log
| time | ts
| text | txt

Telemetry_current

# Configuration

  1.1 Links

https://github.com/GoogleCloudPlatform/google-cloud-iot-arduino

https://console.cloud.google.com/home/dashboard?project=cohesive-photon-227011

https://console.cloud.google.com/iot/registries?project=cohesive-photon-227011&folder&organizationId&pli=1

https://console.cloud.google.com/iot/registries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

## 5 Configuration of Google Cloud

Follow the description on the right-side sidebar on the Google Cloud Platform.

Main steps are:

1. Create project
  a. Name: irrigation
  b. ID: irrigation-229017
  c. Number: 388781223339
2. Turn on Google Cloud APIs (through the tutorial, step 2)
3. Activate a Cloud Shell (cmd prompt)

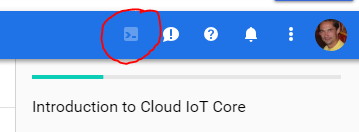
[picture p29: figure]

4. Create topic
  a. Name: irr_topic
5. Clone the Cloud IoT Core Node.js sample files from GitHub
6. Grant permission to the Cloud IoT Core service account
7. Create a device registry
  a. Name: irr-registry
  b. Region: europe-west1
8. Generate keys
9. Create device
  a. Name: irr-device
  b. Registry: irr-registry
  c. Region: europe-west1
10. Connect your device and view telemetry data
11. Create a subscription to the device's topic
  a. Name: projects/irrigation/subscriptions/my-subscription

### 1.1.1 Commands for creation

gcloud pubsub topics create irr-topic

cd ~

rm ~/nodejs-docs-samples/package.json

rm -rf nodejs-docs-samples

git clone https://github.com/GoogleCloudPlatform/nodejs-docs-samples.git

cd ~/nodejs-docs-samples/iot

npm --prefix ./scripts install

node scripts/iam.js irr-topic

gcloud iot registries create irr-registry \

--project=irrigation-229017 \

--region=us-central1 \

--event-notification-config=topic=projects/irrigation-229017/topics/irr-topic

cd ~/nodejs-docs-samples/iot

./scripts/generate_keys.sh

gcloud iot devices create irr-device \

--project=irrigation-229017 \

--region=us-central1 \

--registry=irr-registry \

--public-key \

path=ec_public.pem,type=es256

# To get the 95 char key to use in the Arduino code, ciotc_config.h:

openssl ec -in ec_private.pem -noout -text

cd ~/nodejs-docs-samples/iot/mqtt_example/

npm install

node cloudiot_mqtt_example_nodejs.js \

--projectId=irrigation-229017 \

--registryId=irr-registry \

--deviceId=irr-device \

--privateKeyFile=../ec_private.pem \

--numMessages=5 \

--algorithm=ES256 \

--mqttBridgePort=443

gcloud pubsub subscriptions create \

projects/irrigation-229017/subscriptions/my-subscription \

--topic=irr-topic

# this command is used to pull one or more messages off the stack. Check –help for parameters

gcloud pubsub subscriptions pull --auto-ack \

projects/irrigation-229017/subscriptions/my-subscription \

--limit=50 --sort-by=MESSAGE_ID

# To delete it all again

gcloud pubsub topics list

gcloud iot devices list --region=us-central1 --registry=irr-registry

gcloud iot registries list --region=us-central1

gcloud pubsub subscriptions delete projects/irrigation-229017/subscriptions/my-subscription --quiet

gcloud iot devices delete irr-device \

--region=us-central1 \

--registry=irr-registry --quiet

gcloud iot registries delete irr-registry \

--region=us-central1 --quiet

gcloud pubsub topics delete projects/irrigation-229017/topics/irr-topic --quiet

### 1.1.2 Commands compatible with Arduino Google Cloud library

## 6 Configuration of BigQuery

https://medium.com/google-cloud/build-a-weather-station-using-google-cloud-iot-core-and-mongooseos-7a78b69822c5

#Add permissions for IoT Core

gcloud projects add-iam-policy-binding irrigation-229017 --member=serviceAccount:cloud-iot@system.gserviceaccount.com --role=roles/pubsub.publisher

# Create PubSub topic for device data:

gcloud pubsub topics create telemetry-topic

# Create PubSub subscription for device data:

gcloud beta pubsub subscriptions create --topic telemetry-topic telemetry-subscription

# Create device registry:

gcloud beta iot registries create weather-station-registry --region us-central1 --event-pubsub-topic=telemetry-topic

Overview: https://console.cloud.google.com/iam-admin/iam/project?project=irrigation-229017&orgonly=true

Database: irr_data

Table: raw_data

Link: https://console.cloud.google.com/bigquery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

## 7 Configuration of Firebase

In Google Cloud command shell:

cd ~

npm install -g firebase-tools

functions stop

npm uninstall -g @google-cloud/functions-emulator

npm install -g @google-cloud/functions-emulator

firebase login --no-localhost

# create link to project using the console

https://console.firebase.google.com/u/0/?pli=1 (see screenshot below)

# hereafter add some more features:

firebase init # select all 5 options and use default answers

firebase functions:config:set bigquery.datasetname="irr_data" bigquery.tablename="raw_data"

firebase use –clear

firebase use --add irrigation-229017

firebase use --add

? Which project do you want to add? irrigation-229017

? What alias do you want to use for this project? (e.g. staging) irr_firebase

Created alias irr_firebase for irrigation-229017.

Now using alias irr_firebase (irrigation-229017)

firebase deploy

=== Deploying to 'irrigation-229017'...

i deploying database, storage, firestore, functions, hosting

i database: checking rules syntax...

✔ database: rules syntax for database irrigation-229017 is valid

i storage: checking storage.rules for compilation errors...

✔ storage: rules file storage.rules compiled successfully

i firestore: checking firestore.rules for compilation errors...

i firestore: reading indexes from firestore.indexes.json...

✔ firestore: rules file firestore.rules compiled successfully

i functions: ensuring necessary APIs are enabled...

✔ functions: all necessary APIs are enabled

i storage: uploading rules storage.rules...

i firestore: uploading rules firestore.rules...

Error: HTTP Error: 400, Project 'irrigation-229017' is not a Cloud Firestore enabled project.

firebase deploy --only functions

firebase deploy --only database

firebase deploy --only hosting

firebase deploy --only storage

Link to BigQuery (Firebase project console settings => integrations)

Create database (Firebase project console => Database => create database)

firebase deploy

=== Deploying to 'irrigation-229017'...

i deploying database, storage, firestore, functions, hosting

i database: checking rules syntax...

✔ database: rules syntax for database irrigation-229017 is valid

i storage: checking storage.rules for compilation errors...

✔ storage: rules file storage.rules compiled successfully

i firestore: checking firestore.rules for compilation errors...

i firestore: reading indexes from firestore.indexes.json...

✔ firestore: rules file firestore.rules compiled successfully

i functions: ensuring necessary APIs are enabled...

✔ functions: all necessary APIs are enabled

i storage: uploading rules storage.rules...

i firestore: uploading rules firestore.rules...

✔ firestore: deployed indexes in firestore.indexes.json successfully

i functions: preparing functions directory for uploading...

i hosting[irrigation-229017]: beginning deploy...

i hosting[irrigation-229017]: found 2 files in public

✔ hosting[irrigation-229017]: file upload complete

i database: releasing rules...

✔ database: rules for database irrigation-229017 released successfully

✔ storage: released rules storage.rules to firebase.storage/irrigation-229017.appspot.com

✔ firestore: released rules firestore.rules to cloud.firestore

i hosting[irrigation-229017]: finalizing version...

✔ hosting[irrigation-229017]: version finalized

i hosting[irrigation-229017]: releasing new version...

✔ hosting[irrigation-229017]: release complete

✔ Deploy complete!

… but did not show up in console, so did this:

firebase init functions #overwriting everything

npm install --save @google-cloud/bigquery

npm install cors

edit ~/functions/index.js

# insert the source code from below “You can see the code for the functions above”

# Edits:

# delete last () in line 3 (line with bigquery)

# modify topic name to “irr-topic”

# modify database table fields to the ones used in this project

firebase deploy --only functions

Changes to source code example in …/functions/index.js:

Replace line 3 by these two lines (I think the library has been updated since this examnple was made):

const {BigQuery} = require('@google-cloud/bigquery')

const bigquery = new BigQuery()

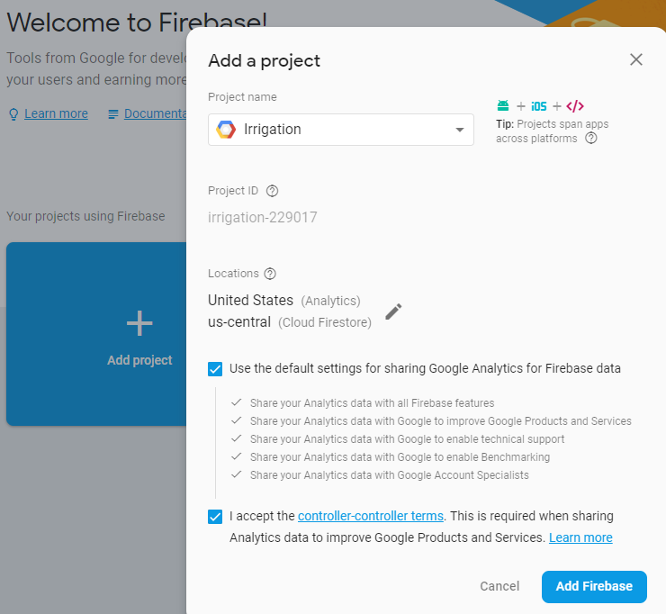
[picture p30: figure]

Project overview: https://console.firebase.google.com/u/0/project/autoirrigation/overview

### 1.1.3 Auth tokens (Database secrets)

Go to Project overview -> Settings -> Service accounts

Copy the “secret” and insert into Arduino code (typically called FIREBASE_AUTH)

## 8 Configuration of Data Studio

https://datastudio.google.com/u/0/navigation/datasources

## 9 Adding new fields in database

### 1.1.4 Device configuration

Data structure is defined in source code files:

- Globals.h
- Persistentmemory.cpp

### 1.1.5 Telemetry data

Defined in

- AutoIrrigation.ino
  - Function CreateTelemetryJson() defines the data transmitted.
- WaterValve.h
- WaterSensor.h
- In Firebase Cloud shell (https://console.cloud.google.com/cloudshell/editor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 )

edit ~/functions/index.js

    - change “const data = {“
- In BigQuery platform (https://console.cloud.google.com/bigquery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 )
- In DataStudio (https://datastudio.google.com/u/0/navigation/datasources )

# Daily use

Using google cloud

Pub/Sub overview: https://console.cloud.google.com/cloudpubsub/topics/irr-topic?project=autoirrigation&orgonly=true

# Reply:

Hi Alvaro,

Thanks for a very good and elaborate example!!!

I made your example work, but only after a few adjustments. The Google + Firebase libraries and tools have probably been updated since this examples was made.

My configuration:

- Instead of your MongooseOS IoT device, I use an Arduino LOLIN (Wemos) D1 R2 mini using the example Esp8266-http.ino from https://github.com/GoogleCloudPlatform/google-cloud-iot-arduino
- BigQuery config: dataset=”irr_data”, table=”raw_data”
- ProjectID= irrigation-229017
- Topic: irr_topic

During configuration of Firebase, I encountered some problems. My complete setup command sequence was this (including a few error messages).

cd ~

npm install -g firebase-tools

functions stop

npm uninstall -g @google-cloud/functions-emulator

npm install -g @google-cloud/functions-emulator

firebase login --no-localhost

# create link to project using the console

https://console.firebase.google.com/u/0/?pli=1 (see screenshot below)

# hereafter add some more features:

firebase init # select all 5 options and use default answers

firebase functions:config:set bigquery.datasetname="irr_data" bigquery.tablename="raw_data"

firebase use –clear

firebase use --add irrigation-229017

firebase use --add

? Which project do you want to add? irrigation-229017

? What alias do you want to use for this project? (e.g. staging) irr_firebase

Created alias irr_firebase for irrigation-229017.

Now using alias irr_firebase (irrigation-229017)

firebase deploy

=== Deploying to 'irrigation-229017'...

i deploying database, storage, firestore, functions, hosting

i database: checking rules syntax...

✔ database: rules syntax for database irrigation-229017 is valid

i storage: checking storage.rules for compilation errors...

✔ storage: rules file storage.rules compiled successfully

i firestore: checking firestore.rules for compilation errors...

i firestore: reading indexes from firestore.indexes.json...

✔ firestore: rules file firestore.rules compiled successfully

i functions: ensuring necessary APIs are enabled...

✔ functions: all necessary APIs are enabled

i storage: uploading rules storage.rules...

i firestore: uploading rules firestore.rules...

Error: HTTP Error: 400, Project 'irrigation-229017' is not a Cloud Firestore enabled project.

firebase deploy --only functions

firebase deploy --only database

firebase deploy --only hosting

firebase deploy --only storage

Link to BigQuery (Firebase project console settings => integrations)

Create database (Firebase project console => Database => create database)

firebase deploy

=== Deploying to 'irrigation-229017'...

i deploying database, storage, firestore, functions, hosting

i database: checking rules syntax...

✔ database: rules syntax for database irrigation-229017 is valid

i storage: checking storage.rules for compilation errors...

✔ storage: rules file storage.rules compiled successfully

i firestore: checking firestore.rules for compilation errors...

i firestore: reading indexes from firestore.indexes.json...

✔ firestore: rules file firestore.rules compiled successfully

i functions: ensuring necessary APIs are enabled...

✔ functions: all necessary APIs are enabled

i storage: uploading rules storage.rules...

i firestore: uploading rules firestore.rules...

✔ firestore: deployed indexes in firestore.indexes.json successfully

i functions: preparing functions directory for uploading...

i hosting[irrigation-229017]: beginning deploy...

i hosting[irrigation-229017]: found 2 files in public

✔ hosting[irrigation-229017]: file upload complete

i database: releasing rules...

✔ database: rules for database irrigation-229017 released successfully

✔ storage: released rules storage.rules to firebase.storage/irrigation-229017.appspot.com

✔ firestore: released rules firestore.rules to cloud.firestore

i hosting[irrigation-229017]: finalizing version...

✔ hosting[irrigation-229017]: version finalized

i hosting[irrigation-229017]: releasing new version...

✔ hosting[irrigation-229017]: release complete

✔ Deploy complete!

… but did not show up in console, so did this:

firebase init functions #overwriting everything

# ***** IMPORTANT *****

npm install --save @google-cloud/bigquery

npm install cors

# ***** IMPORTANT *****

# Finally I had to do a little, but crucial change to the source code in …/functions/index.js:

edit ~/functions/index.js

# insert the source code from below “You can see the code for the functions above”

# Edits:

Replace line 3 by these two lines (I think the library has been updated since this examnple was made):

const {BigQuery} = require('@google-cloud/bigquery')

const bigquery = new BigQuery()

# modify topic name to “irr-topic”

# modify database table fields to the ones used by your IOT device

firebase deploy --only functions

# Wrapping

Print from PCBNEW:

Front:

- Blue2 copper layer
- Edge cut
- F. crtyrd
- F. fab

Back:

- All copper layers
- Edge cut
- MIRROR

# PCB integration in 3D print

## 10 Export PCB (wrap) layout from kiCad to Fusion360

1. In KiCAD: File => plot => DXF format. Choose only the courtyard layer

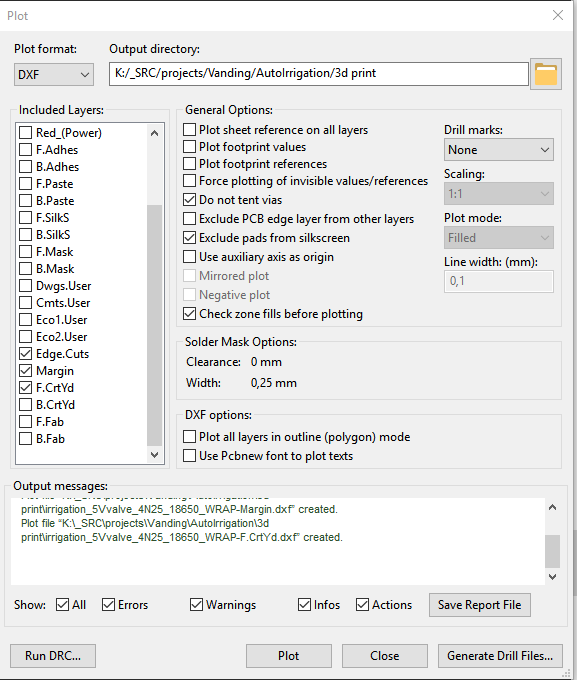
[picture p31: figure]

2. In Fusion360:
  a. Open the DXF file just created (open into a new drawing)
  b. Copy all elements from this drawing
  c. Edit the sketch for the PCB board
  d. Paste into the sketch

# 3D printed case

Order of design

1. Model each hardware component. Placed in separate proejcts.
2. Import needed
3. Place them physically as wished
4. Create base floor. Project spefici markers from the needed components – nothing else.

# 3D printing of PCB board

## 11 Settings

Setup -> Pad to mask clearance:


## 12 Export to Gerber files

File -> Plot


Drill holes:


Export as SVG

Import with 0.096 as scaling factor (don’t know why)

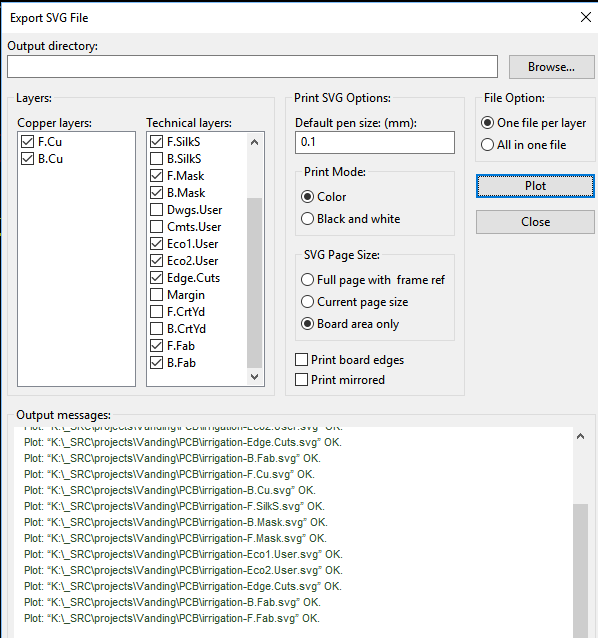
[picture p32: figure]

# Excel interface

https://bigquery-connector.appspot.com/

Use this unique key to run queries against BigQuery:

MCY6GsxRirTgTZNhLWcm2ILOlGUxHZgG8wdlNB9LPcUS7MZkOw6uyxIE8vzAO+NHog9L97z/qE17wa9hjj06dVXI+oOMZgSTonmZw/lDouQpiHMVmjMiFU60jQwGn8GmcQYiV99pVsXNgaunSq6YDpTubG+TE7D7fAs4IefKQf/9YM1U9Tp1/FjhVxZ29+fGabpn1Tm2/YmEViEkIt0yaw==

This key expires on Thursday, February 7, 2019 2:49:02 AM PST.

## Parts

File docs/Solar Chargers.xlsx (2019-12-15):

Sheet: needs
eff. battery capacity [mAh @ 3.7V] | Panel | Rated max [V] | Ratex max [W] | output [mA] INDIRECT sun | output [W] | Hours to charge fully | Days @ 6h/day | output [mA] DIRECT sun | output [W] | Hours to charge fully | Days @ 6h/day
2880 | 110x69 | 5 | 1.25 | 5 | 0.0185 | 576 | 96 | 150 | 0.555 | 19.2 | 3.2

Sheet: chargers
link | model | pris | mAh | battery type | output | recharg iphone 4S x | solar | USB output | charge time | vægt | dim
http://www.scosche.com/consumer-tech/product/2073 | goBAT II - Portable Charger & Backup Battery | 330 | 5000 | 3.7v - 50000mA Lithium polymer | 5v – 5000mAh | 2.6 | no | 2
http://www.amazon.com/Xantrex-Technologies-852-2071-Powerpack-Inverter/dp/B000SECKO2 | Xantrex Technologies 852-2071 Xpower AC/DC Powerpack Solar | 1809.5 |  |  | 5.5V, 900mA |  | yes
http://www.voltaicsystems.com/amp.shtml | Voltaic Amp Solar Charger | 544.5 | 3000 |  | 4w |  | yes | 1 | 4-5 h | 480g | 16.5 x 14.5 x 4 cm
http://www.rosebikes.dk/product/detail/id:509853?gclid=CI6Q-JSgmbECFUK-zAod-Sz4mw | A-SOLAR AM-403 POWER PACK | 460 | 1600 |  | 1000 |  | yes |  |  | 90
http://www.a-solar.eu/EN/a-solar_power_dock_for_iphone_ipad.htm | Power Dock for iPhone/ iPad (AM406) | 869 | 6000 |  | 5V / 2.1A | 3-4 h | yes |  | 4 h | 210
http://www.mytrendyphone.dk/shop/a-solar-al-260-power-73510p.html?network=KELKOODA&sstlcmpid=9433 | A-Solar AL-260 Power Bank | 299 | 2400 |  | 5.5V / 500mAh |  | yes |  |  | 90
 | A-Solar Micro Oplader AM-500 |  | 1900 |  | 5.5V / 500mAh | 3 | yes |  | 20 h

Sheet: solar panels
Link | Nom. Cap. [V] | Max power [W] | height | width | max mA | wH / day | Daily sun hours | 6
https://www.aliexpress.com/item/ANBES-Solar-Panel-5V-6V-12V-Mini-Solar-System-DIY-For-Battery-Cell-Phone-Chargers-Portable/32848710253.html | 6 | 0.6 | 80 | 55 |  | 2.7
https://www.aliexpress.com/item/ANBES-Solar-Panel-5V-6V-12V-Mini-Solar-System-DIY-For-Battery-Cell-Phone-Chargers-Portable/32848710253.html | 6 | 0.6 | 90 | 55
 | 5 | 1.25 | 110 | 69

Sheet: angling and location
https://sinovoltaics.com/learning-center/system-design/solar-panel-angle-tilt-calculation/
Latitude | 55.676098
Summer factor | -23.5
Best angle (summer) | 26.6084882

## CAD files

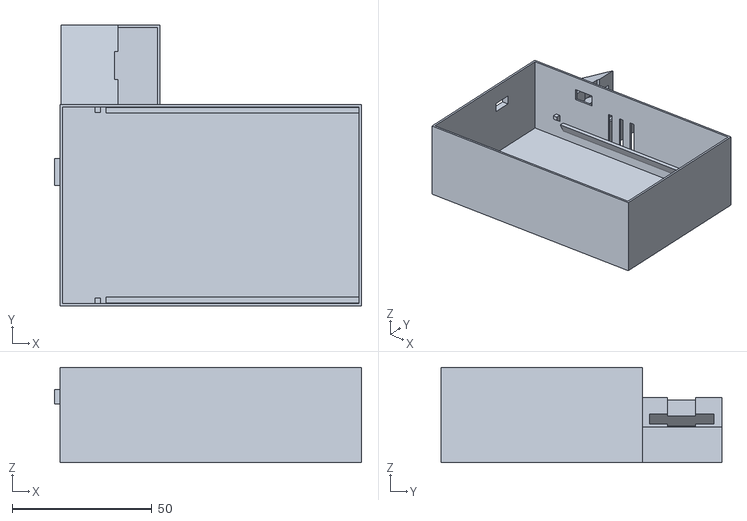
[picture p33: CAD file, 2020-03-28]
3d print/Irrigation unit - Main box (side mounted) v21.stl
109.7 x 100.6 x 34.0

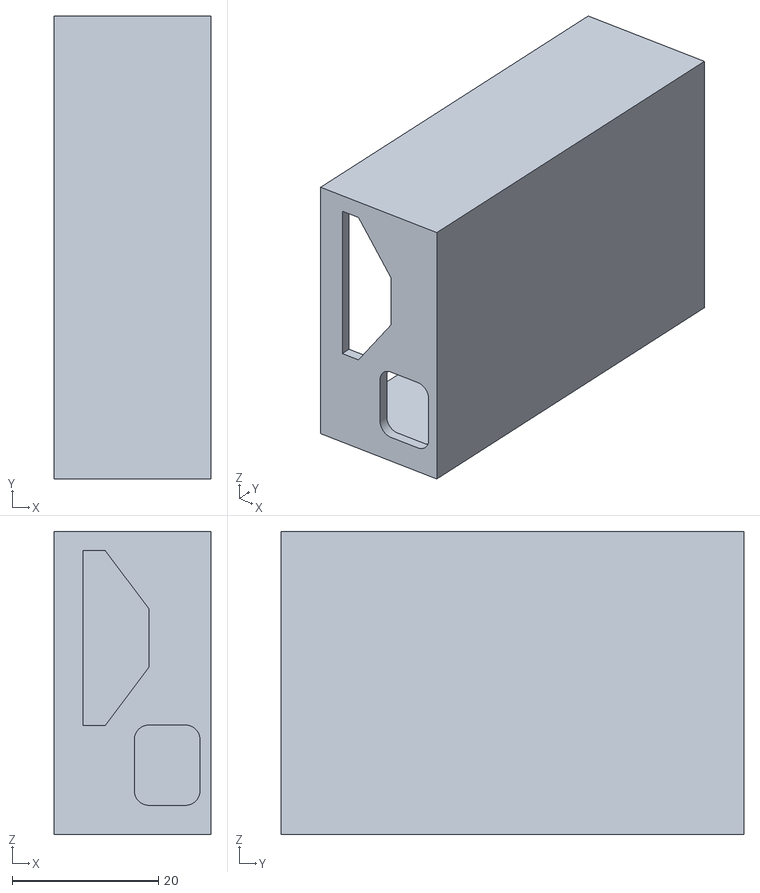
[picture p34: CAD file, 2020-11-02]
3d print/Simple sensor - top v5.stl
21.5 x 63.4 x 41.5

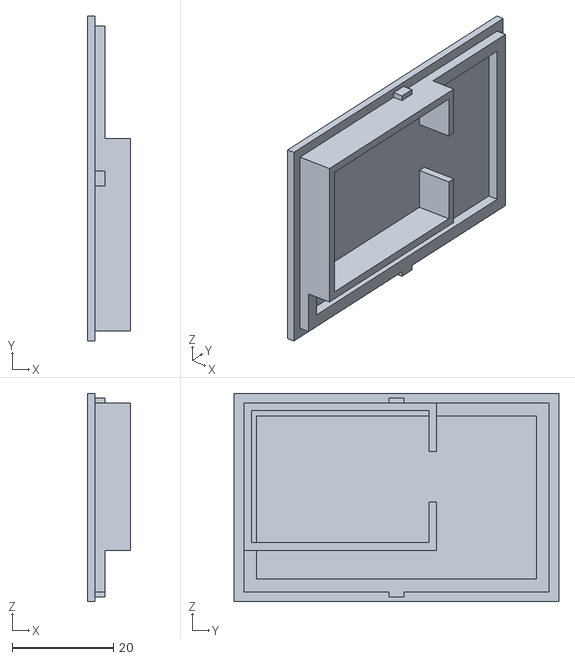
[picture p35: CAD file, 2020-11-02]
3d print/Simple sensor - bottom v4.stl
8.50 x 64.0 x 41.0

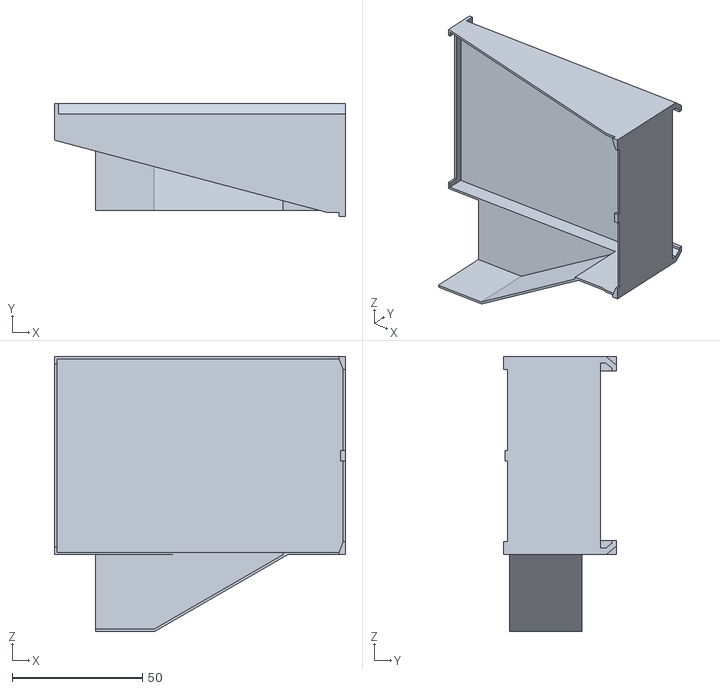
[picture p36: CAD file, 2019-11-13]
3d print/Roof v17.stl
111.5 x 43.2 x 105.4

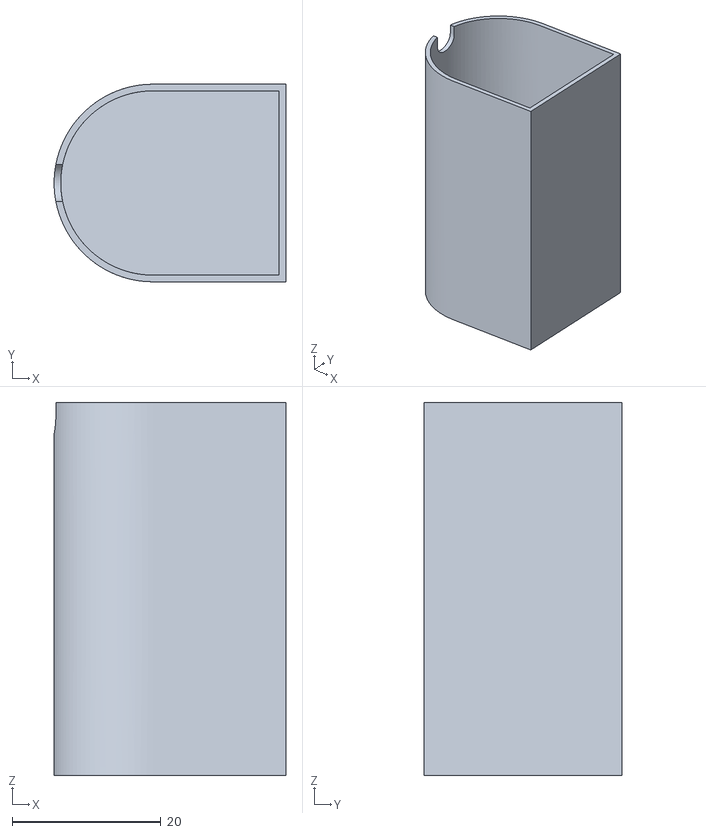
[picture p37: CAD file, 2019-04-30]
3d print/Valve unit v4.stl
31.2 x 26.6 x 50.2

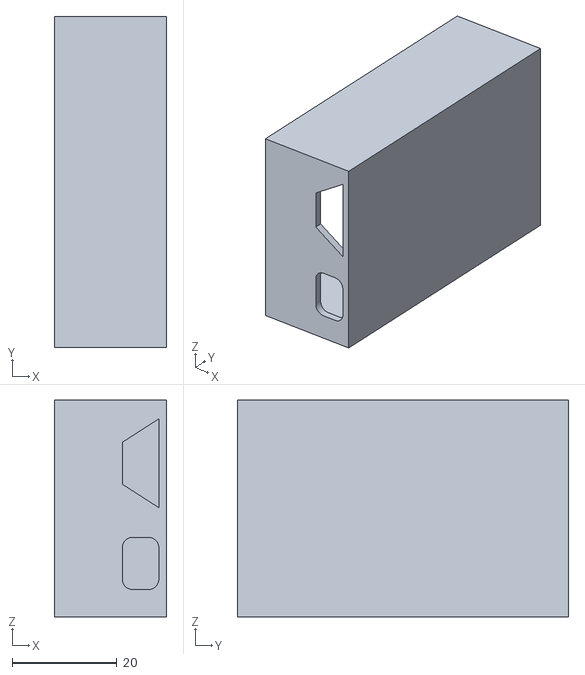
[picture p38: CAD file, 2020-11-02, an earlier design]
3d print/Simple sensor - top v2.stl
21.5 x 63.4 x 41.5

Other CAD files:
3d print/Irrigation unit - Main box (side mounted) v17.stl
3d print/Simple sensor - bottom v2.stl
3d print/Simple sensor - top v3.stl
3d print/Simple sensor - top v4.stl
3d print/fusion360 export/Irrigation unit - Main box (side mounted) v18.f3z
3d print/fusion360 export/Irrigation unit - valve box v5.f3z
3d print/fusion360 export/_ 12V valve v2.f3d
3d print/fusion360 export/_ 5V mini valve v1.f3d
3d print/fusion360 export/_ DCDC step down converter v1.f3d
3d print/fusion360 export/_ PCB board for Irrigation unit v2.f3d
3d print/fusion360 export/_ Rectangular On-off switch v1.f3d
3d print/fusion360 export/_ Solar panel (ZW 110x69) v3.f3d
3d print/fusion360 export/_ capacitive soil humidity sensor v5.f3d
3d print/fusion360 export/_ humidity sensor v14.f3d

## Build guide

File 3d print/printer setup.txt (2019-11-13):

Tape:
langs HELE kanten (½-1 cm)
helt ud i hjørnerne
midt ingenting 

Heat:
150W halogene lamp

Import: auto repair OK

Rotate:
 x 270 deg
 z 90 deg

Print setup:
print type: high detail
Rim: no
Raft: no
Support: no
Layer height: 0.3
Speeed: slow
Temp: -5
retract len: 4
retract speed: 30
surface ironing: NO

No supports

Est time: 4:30 (beregnet). Genberegnes til 3 timer
filmaent usage: 8,4m

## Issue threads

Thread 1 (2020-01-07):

hardware question

bobkelso974, 2020-01-07:
Hello,
I am interested in your project.
I would like to do the same but replacing the valve with a water pump.
I have a question about the valve....
You indicate "The valve and valve driver (which is a 5V => 12V converter)" When is the valve powered by 12v? With the J5019? and when do you use the step down? I haven't seen it on your file: irrigation v6.0.sch
Thanks for your help

ratnick, 2020-01-07:
I realize that there's something missing in the v5.3 sch file. Originally I designed this for 5V valves, but they were not powerful enough to drive water (they were ment for gas/air). So I changed that very late in the project to 12V by doing another up-conversion in the actual 3D printed valve unit with another J5019 (see pic https://github.com/ratnick/AutoIrrigation/blob/master/media/d5a75f028147682061810ceb927edf5d.png).
So in version 5.3, there are two up-conversion: from battery (4.xV) to 5V outlet, and then to 12V after the TIP120 inside the valve unit.

In 6.0 I reverse this to get away from electronics in the valve unit. First up to 12V, and then down to 5V. I'm no expert if this is more efficient (please comment), but it just seems like a better thing to do.

6.0 has never been PCB printed, and hence not tested. 5.3 works.

Makes sense?

bobkelso974, 2020-01-08:
thanks for these informations
Using 12 V for the valve(version 5.3), does it work well over time?

ratnick, 2020-01-08:
There are many perspectives of that question :-)
- The valve use quite a lot of power when on. Therefore water pressure should be as high as possible, yet operable for the valve. In my case, about 30 seconds watering per day is more than enough, even on sunny days. The beauty is that the solar panels also produce more power on sunny days.
- I have had the system running in regular operation for at least a month over the summer without running flat on batteries. But it's been a quite wet summer in Denmark, so I have not been able to test it over a longer hot and dry period. I guess it will work fine, though.
- I have observed that one of the J5019's started to generate a high pitch sound after some weeks. I don't know why, but I had 3 devices, and this only happened on one.

bobkelso974, 2020-01-09:
Thank you for all the answers!!

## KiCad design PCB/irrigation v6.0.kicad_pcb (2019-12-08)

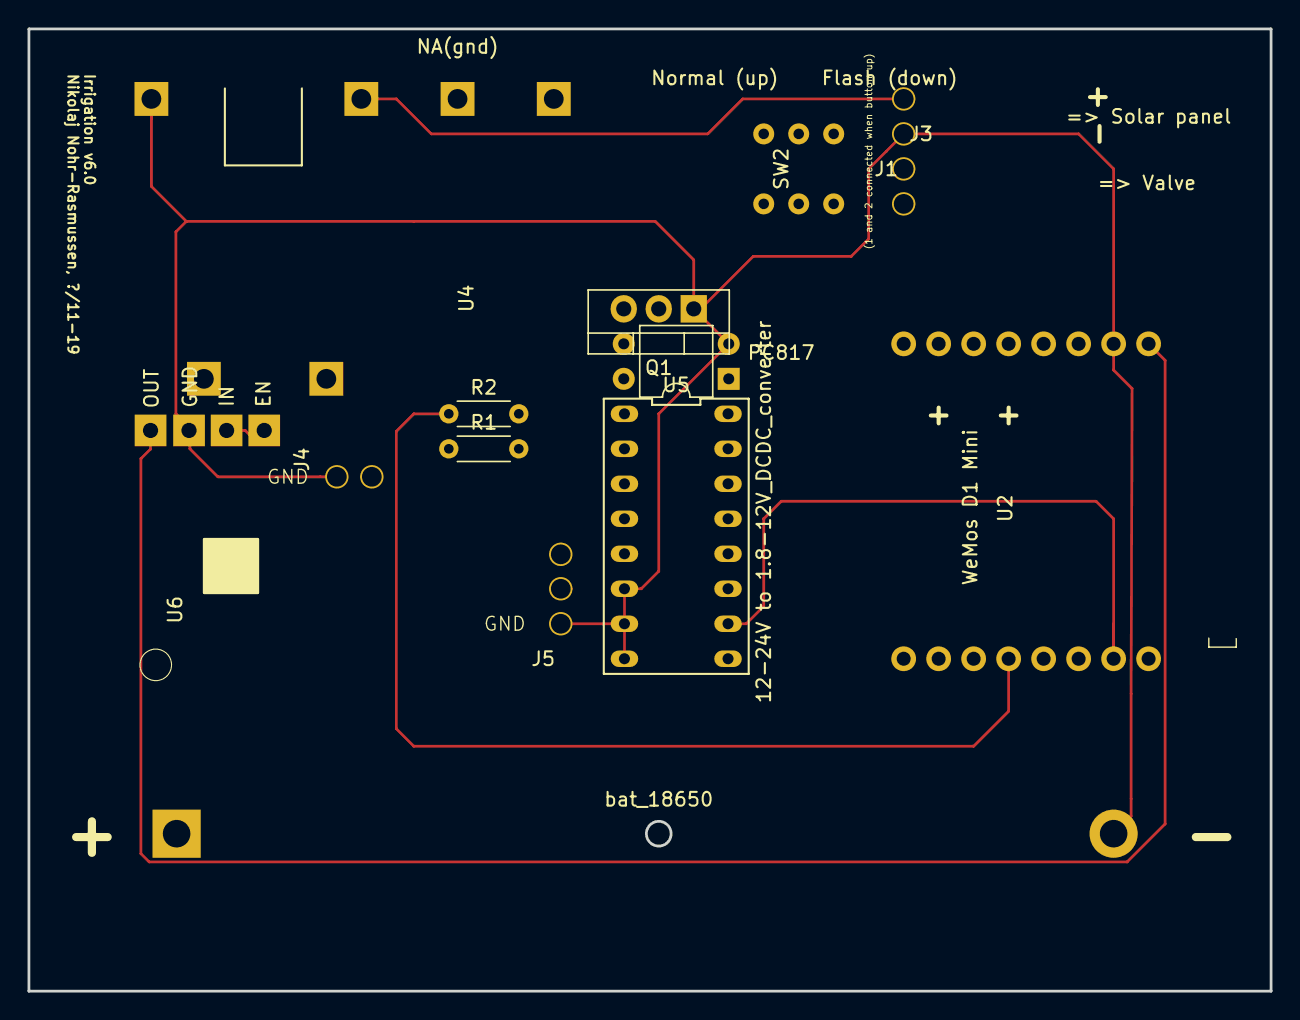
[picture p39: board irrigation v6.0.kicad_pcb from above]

Board: 6 copper layers, 90.2 x 69.8 mm, 14 parts (0 on the bottom side), 9 nets.

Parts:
J1: => Solar panel; 2p_connector_v2
J3, J4: => Valve; 2p_connector_v2
J5: Capacitive soil sensor; 3p_connector_v1
Opto1: PC817; DIP-4_W7.62mm
Q1: TIP120; TO-220-3_Vertical
R1: 100k; R_Axial_DIN0204_L3.6mm_D1.6mm_P5.08mm_Horizontal
R2: 5k; R_Axial_DIN0204_L3.6mm_D1.6mm_P5.08mm_Horizontal
SW2: flash; onoff_push_button_2x3_pins_v2
U2: 12-24V to 1.8-12V_DCDC_converter; D1_mini_board_v10
U4: CD4052B; J5019_v5
U5: CD4052B; 74HC4052_analogue_mux_v1
U6: 12-24V-1.8-12V_DCDC_converter; 12-5V_DCDC_v2
bat_18650: Battery_Cell; BatteryHolder_MPD_BH-18650-PC2_v4

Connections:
/5V: Opto1.4, U2.1, U6.1
/12V: J3.2, U2.3, U2.4, U6.3, U6.4
GND: J1.1, J5.1, Opto1.2, Q1.3, U2.2, U4.6, U5.6, U5.7, U5.8, U6.2, bat_18650.2
unnamed: J3.1, Q1.2
unnamed: J4.2, bat_18650.1
unnamed: J5.2, Opto1.3, U5.16
unnamed: J5.3, U5.12
unnamed: Q1.1, R2.2
unnamed: R1.2, U5.14

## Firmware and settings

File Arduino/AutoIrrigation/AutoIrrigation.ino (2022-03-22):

/*
    Name:       AutoIrrigation.ino
    Created:	17-09-2018 15:08:50
    Author:     Nikolaj Nøhr-Rasmussen
*/

// Including the libraries below, allows to turn off Deep Search in libraries => faster compiling
#include "FirebaseModel.h"
#include "NNR_FirebaseDatabase.h"
#include "NNR_Firebase_PersistentMemory.h"
#include <jsmn.h>
#include <FirebaseJson.h>
#include <NNR_Wifi.h>
#include <SysCall.h>
#include <sdios.h>
#include <BlockDriver.h>
#include <SDFSFormatter.h>
#include <SdFatConfig.h>
#include <SdFat.h>
#include <MinimumSerial.h>
#include <FreeStack.h>
#include <SDFS.h>
#include <SD.h>
#include <FirebaseJson.h>    // works with 2.2.8, but NOT 2.3.9. This will give random errors in communication with Firebase. I think it's becaise FirebaseJSON struct or class is changed
// end 

// OTA upload
#include <LEAmDNS_Priv.h>
#include <ArduinoOTA.h>
// end

#include "compile_flags.h"

#ifdef USE_WIFI
#include <FirebaseESP8266.h>
#include <ESP8266WiFi.h>
#include <WiFiUdp.h>
#include <WiFiServer.h>
#include <WiFiClient.h>
#endif

#ifdef USE_FIREBASE
#include <SPI.h>
#include <FirebaseESP8266HTTPClient.h>
#endif


#include <SoftwareSerial.h>
#include <Wire.h>
#include <DHTesp.h>
#include <EEPROM.h>
#include <TimeLib.h>        // http://playground.arduino.cc/code/time - installed via library manager
#include <time.h>

// own libraries
#include "globals.h"
#include "ciotc_config.h" // Wifi configuration here
#include "cli.h"
#include "NNR_PersistentMemory.h"
#include <NNR_DeepSleep.h>
#include "NNR_LEDHandler.h"
#include "NNR_OTAupdate.h"
#include <NNR_Logging.h>
#include "AnalogMux.h"
#include "SoilHumiditySensor.h"
#include "DistanceSensor.h"
#include "VoltMeter.h"
#include "Thermometer.h"
#include "serialPortHandler.h"
#include "WaterValve.h"


#ifdef USE_AZURE
#include "AzureCloudHandler.h"
#endif
#ifdef USE_GAS_SENSOR
#include "GasSensor.h"
GasSensorClass gasSensor;
#endif

// Wifi and network globals
Device device;
const char timeServer[] = "0.dk.pool.ntp.org"; // Danish NTP Server 
byte localmacAddr[6];
int wifiIndex = 0;

/*
//Hardware pin configuration on WeMOS D1
const int MUX_S0 = D8; // S0 = Pin A on schematic
const int MUX_S1 = D7; // S1 = Pin B on schematic
const int HUM_SENSOR_PWR_CTRL = D1;
const int VALVE_CTRL = D5;
const int DHT11_SIGNAL_PIN = D6;
const int ANALOG_INPUT = A0;
// MUX channels X0, X1, X2... on schematic
const int CHANNEL_HUM = 0;
const int CHANNEL_BATT = 1;
const int CHANNEL_WATER = 2;
const int CHANNEL_TEMPERATURE = 2;
*/

// Sensors and actuators
DistanceSensorClass sensorA;
SoilHumiditySensorClass soilHumiditySensorA;
WaterValveClass waterValveA;
VoltMeterClass externalVoltMeter;
ThermometerClass thermometer;
const int VALVE_OPEN_DURATION = 2;   // [2] time a valve can be open in one run-time cycle, i.e. between deepsleeps
const int VALVE_SOAK_TIME     = 3;   // [30] time between two valve openings

// General control
int loopCount = 0;  // used in conjunction with NBR_OF_LOOPS_BEFORE_SLEEP

#ifdef USE_GOOGLE_CLOUD
// Google Cloud globals
CloudIoTCoreDevice *device;
#endif

#ifdef USE_FIREBASE
#define FIREBASE_HOST "irrfire.firebaseio.com" 
#define FIREBASE_AUTH "w3Q5F3zWG3RkudEjGUJZVi2wiVDvZCKY3VkVywkC"
//#define FIREBASE_AUTH "QhxlUMo2PjjqCTFwgVLInGH7lFPEA8oSKhoMG76e"
#define FB_DEVICE_PATH "/irrdevices/"
String FB_BasePath;
FirebaseData firebaseData; // FirebaseESP8266 data object
boolean firstRun = true;
#endif

const int JSON_BUFFER_LENGTH = 250;

void InitUnitTest();

void ConnectToWifi() {
	int wifiIndex = initWifi(PersistentMemory.ps.wifiSSID, PersistentMemory.ps.wifiPwd, &device.wifi);
	delayNonBlocking(250);
	if (wifiIndex == -1 || WiFi.status() != WL_CONNECTED) {
		LogLine(0, __FUNCTION__, "Could not connect to wifi. ", false);
	}
	else if (wifiIndex == 100 || wifiIndex == 200) {
		// Connected. Do nothing.
	}
	else {   // then we have swapped SSID. Update persistent memory so we keep using the new hotspot
		PrintIPAddress();
		PersistentMemory.SetwifiSSID(device.wifi.currentSSID);
		PersistentMemory.SetwifiPwd(device.wifi.pwd);
	}
}

boolean WaterIfNeeded() {
	int del;
	float vccTmp;
	boolean valveWasOpened = false;

	vccTmp = externalVoltMeter.ReadVoltage();
	// update persistent memory in case something has changed
	PersistentMemory.ps.lastVccSummarizedReading = externalVoltMeter.lastSummarizedReading;
	PersistentMemory.WritePersistentMemory();
	LogLinef(3, __FUNCTION__, "Voltage reading %f", vccTmp);

	LED_Flashes(1, 300);
	if ((soilHumiditySensorA.CheckIfWater() == SoilHumiditySensor.DRY) || SIMULATE_WATERING) {
		LogLine(1, __FUNCTION__, "Low water detected. Watering and soaking.");

		waterValveA.OpenValve();
		UploadTelemetry_();
		waterValveA.KeepOpen();

		waterValveA.CloseValve();
		UploadTelemetry_();
		valveWasOpened = true;
	}
	if (!valveWasOpened) {
		LogLine(1, __FUNCTION__, "High water detected. Skip watering and soaking.");
		UploadTelemetry_();
	}
	return valveWasOpened;
}


boolean IsPersistentMemorySet() {
	// Check if values are reasonable. Not bullit proof!
//dbg1	return (PersistentMemory.GetCloudUsername().equals("initial value"));
	return true;
}

void InitPersistentMemoryIfNeeded() {
	if (!IsPersistentMemorySet() || FORCE_NEW_VALUES) {
		PersistentMemory.init(true, TOTAL_SECS_TO_SLEEP, DEVICE_ID, HARDWARE_DESCRIPTION, DefaultRunmode.c_str(), VALVE_OPEN_DURATION, VALVE_SOAK_TIME, LOOP_DELAY, DEBUGLEVEL);   // false: read from memory.  true: initialize
		WiFi.macAddress(localmacAddr);
		PersistentMemory.SetmacAddress(localmacAddr);
		#if defined (USE_DEEP_SLEEP)
			PersistentMemory.SetdeepSleepEnabled(true);
		#else
			PersistentMemory.SetdeepSleepEnabled(false);
		#endif
	}
}

boolean first = true;

#ifdef USE_FIREBASE

boolean IsSettingsDataUpdatedByUser() {
	String s = FB_BasePath + "/settings/" + FB_UserUpdate;
	if (Firebase.getBool(firebaseData, s)) {
		if (firebaseData.boolData()) {
			LogLinef(2, __FUNCTION__, "true - %s  " , s.c_str());
			return true;
		}
		else {
			LogLinef(4, __FUNCTION__, "false (not set by user) - %s   ", s.c_str());
		}
	}
	else {
		LogLinef(5, __FUNCTION__, "false (data does not exist in Firebase) - %s + %s", s.c_str(), firebaseData.errorReason().c_str());
	}
	return false;
}

boolean DeviceExistsInFirebase() {
	Serial.println(FB_BasePath + "/state/" + FB_wifiSSID);
	if (!Firebase.getString(firebaseData, FB_BasePath + "/state/" + FB_wifiSSID)) {
		//UploadLog_("Device seems not to exist. Double checking.");
		Serial.println("X2");
		PersistentMemory.PrintpsRAW();
		Serial.println("X3");
		if (!Firebase.getString(firebaseData, FB_BasePath + "/metadata/" + FB_macAddress)) {
			LogLine(0, __FUNCTION__, "** Device does not exist");
			return false;
		}
	}
	return true;
}

void GetSettingsFromFirebase_(boolean &firstRun) {
	int val;
	boolean b;
	String str;

	LogLine(4, __FUNCTION__, "begin");
	if (firstRun || IsSettingsDataUpdatedByUser()) {
		LogLinef(5, __FUNCTION__, "2 %s  ", FB_BasePath.c_str());
		str = FB_BasePath + "/metadata/" + FB_deviceLocation;


		if (Firebase.getString(firebaseData, str)) {
			PersistentMemory.SetdeviceLocation(firebaseData.stringData());
			LogLinef(5, __FUNCTION__, " %s = %s", FB_deviceLocation, firebaseData.stringData().c_str());
		}

		// update firebase with IP address. We use the diviceID for this to be able to identify the device for OTA updates
		Firebase.setString(firebaseData, FB_BasePath + "/metadata/" + FB_deviceID, PersistentMemory.GetDeviceID());
		if (Firebase.getString(firebaseData, FB_BasePath + "/metadata/" + FB_deviceID)) {
			PersistentMemory.SetdeviceID(firebaseData.stringData()); 
			LogLinef(5, __FUNCTION__, " %s = %s", FB_deviceID, firebaseData.stringData().c_str());
		}
		if (Firebase.getInt(firebaseData, FB_BasePath + "/settings/" + FB_mainLoopDelay)) {
			PersistentMemory.SetmainLoopDelay(firebaseData.intData());
			LogLinef(5, __FUNCTION__, " %s = %s", FB_mainLoopDelay, firebaseData.stringData().c_str());
		}
		if (Firebase.getInt(firebaseData, FB_BasePath + "/settings/" + FB_debugLevel)) {
			int d = firebaseData.intData();
			PersistentMemory.SetdebugLevel(d);
			SetFBDebugLevel(d);
			LogLinef(5, __FUNCTION__, " %s = %d", FB_debugLevel, firebaseData.intData());
		}
		String fullPath;
		for (int i = 0; i < MAX_WAKEUPTIMES; i++) {
			fullPath = FB_BasePath + "/settings/" + FB_wakeupTime + String(i);
			if (Firebase.getString(firebaseData, fullPath)) {
				LogLinef(5, __FUNCTION__, " %s = %s", fullPath.c_str(), firebaseData.stringData().c_str());
				PersistentMemory.SetWakeTime(i, firebaseData.stringData());
			}
		}
		if (Firebase.getString(firebaseData, FB_BasePath + "/settings/" + FB_pauseWakeTime)) {
			LogLinef(5, __FUNCTION__, " %s = %s", FB_pauseWakeTime, firebaseData.stringData().c_str());
			PersistentMemory.SetPauseWakeTime(firebaseData.stringData());
		}
		if (Firebase.getBool(firebaseData, FB_BasePath + "/settings/" + FB_deepSleepEnabled)) {
			b = firebaseData.boolData();
			PersistentMemory.SetdeepSleepEnabled(b);
			LogLinef(5, __FUNCTION__, " %s = %b", FB_deepSleepEnabled, b);
		}
		if (Firebase.getString(firebaseData, FB_BasePath + "/settings/" + FB_runMode)) {
			PersistentMemory.SetrunMode(firebaseData.stringData());
			LogLinef(5, __FUNCTION__, " %s = %s", FB_runMode, firebaseData.stringData().c_str());
		}
		if (Firebase.getInt(firebaseData, FB_BasePath + "/settings/" + FB_totalSecondsToSleep)) {
			PersistentMemory.SettotalSecondsToSleep(firebaseData.intData());
		}
		if (Firebase.getInt(firebaseData, FB_BasePath + "/settings/" + FB_valveOpenDuration)) {
			val = firebaseData.intData();
			PersistentMemory.SetvalveOpenDuration(val);
			waterValveA.SetvalveOpenDuration(val);
		}
		if (Firebase.getInt(firebaseData, FB_BasePath + "/settings/" + FB_humLimit)) {
			val = firebaseData.intData();
			PersistentMemory.SethumLimit(val);
			soilHumiditySensorA.SethumLimitPct(val);
		}
		if (Firebase.getFloat(firebaseData, FB_BasePath + "/settings/" + FB_vccAdjustment)) {
			float f = firebaseData.floatData();
			PersistentMemory.SetvccAdjustment(f);
		}
		if (Firebase.getFloat(firebaseData, FB_BasePath + "/settings/" + FB_vccMinLimit)) {
			float f = firebaseData.floatData();
			PersistentMemory.SetvccMinLimit(f);
		}

		if (Firebase.getInt(firebaseData, FB_BasePath + "/settings/" + FB_valveSoakTime)) {
			val = firebaseData.intData();
			LogLinef(5, __FUNCTION__, " %s = %d", FB_valveSoakTime, val);
			PersistentMemory.SetvalveSoakTime(val);
			waterValveA.SetvalveSoakTime(val);
		}

		if (Firebase.getBool(firebaseData, FB_BasePath + "/settings/" + FB_runOTAupdate)) {
			b = firebaseData.boolData();
			PersistentMemory.SetRunOTA(b);
			LogLinef(5, __FUNCTION__, " %s = %b", FB_runOTAupdate, b);
		}

		Firebase.setBool(firebaseData, FB_BasePath + "/settings/" + FB_UserUpdate, false);
		LogLinef(4, __FUNCTION__, " %s = %s", FB_deviceID, PersistentMemory.GetDeviceID().c_str());

		PersistentMemory.Printps();
		LogLine(2, __FUNCTION__, "New settings read");
		firstRun = false;
	}
}

void CreateNewDevice() {
	FirebaseJson jsoMetadata;
	FirebaseJson jsoState;
	FirebaseJson jsoSettings;
	FirebaseJson jsoDummy;
	bool res;

	InitPersistentMemoryIfNeeded();

	AddMetadataJson(&jsoMetadata, &PersistentMemory.ps);
	AddStateJson(&jsoState, &PersistentMemory.ps);
	AddSettingsJson(&jsoSettings, &PersistentMemory.ps);

	res = SendToFirebase(set, "metadata", jsoMetadata, firebaseData);
	res = SendToFirebase(set, "state", jsoState, firebaseData);
	res = SendToFirebase(set, "settings", jsoSettings, firebaseData);

	// add some dummies so we can use "push" consistently for log and telemetry
	jsoDummy.set("x", "-");
	res = SendToFirebase(set, "log", jsoDummy, firebaseData);

}

void UploadStateAndSettings_(boolean &firstRun) {

	LogLine(4, __FUNCTION__, "begin");

	// Check if device has been created. 
	// If it exists, read current state values from Firebase into persistent memory, otherwise create it. 
	if ( DeviceExistsInFirebase() ) {
		GetSettingsFromFirebase_(firstRun);
		InitFirebaseLogging(firebaseData, FB_BasePath, "log", JSON_BUFFER_LENGTH);
	}
	else {
		CreateNewDevice();
		InitFirebaseLogging(firebaseData, FB_BasePath, "log", JSON_BUFFER_LENGTH);   //nnr +
		LogLinef(4, __FUNCTION__, "%s created", FB_BasePath.c_str());
	}
}

void RemoveTelemetryFromFirebase() {
	String s = FB_BasePath + "/telemetry";
	LogLine(2, __FUNCTION__, "	removing telemetry");
	Firebase.deleteNode(firebaseData, s);
}

void RemoveDummiesFromFirebase(String path) {
	String s = FB_BasePath + path;   // "/telemetry/x";
	String res;
	if (Firebase.getString(firebaseData, s)) {
		LogLinef(4, __FUNCTION__, "dummy exists. Will remove it. path=%s ", s.c_str());
		Firebase.deleteNode(firebaseData, s);
	}
	else {
		LogLine(4, __FUNCTION__, "dummy did not exist");
	}
}

#endif

void UploadTelemetry_() {

	FirebaseJson jsoTelemetry;
	FirebaseJson jsoTeleTimestamp;
	boolean newTelemetry = true;  // so far only used for gassensor
	bool res;

	LogLine(4, __FUNCTION__, "begin");
	// Build the telemetry. This is partly dependent on which sensors are present.

	#if defined(USE_GAS_SENSOR)
		newTelemetry = gasSensor.GetTelemetryJson(&jsoTelemetry);
		LogLine(4, __FUNCTION__, "telemetry fetched from gas sensor");
	#elif defined(USE_DHT11_SENSOR)
		thermometer.AddTelemetryJson(&jsoTelemetry);
		LogLine(5, __FUNCTION__, "telemetry fetched from DHT11 sensor");
//211009		externalVoltMeter.AddTelemetryJson(&jsoTelemetry);
//		LogLine(5, __FUNCTION__, "telemetry fetched from Voltmeter");
	#elif defined(USE_DISTANCE_SENSOR)
		sensorA.AddTelemetryJson(&jsoTelemetry);
		externalVoltMeter.AddTelemetryJson(&jsoTelemetry);
		LogLine(5, __FUNCTION__, "telemetry fetched from DISTANCE sensor");
	#else
		soilHumiditySensorA.AddTelemetryJson(&jsoTelemetry);
		waterValveA.AddTelemetryJson(&jsoTelemetry);
		externalVoltMeter.AddTelemetryJson(&jsoTelemetry);
	#endif
		#ifdef USE_FIREBASE
			int32_t wifiStrength = WiFi.RSSI();
			jsoTelemetry.add(FB_wifi, wifiStrength);
			if (newTelemetry) {
				res = SendToFirebase(set, "telemetry_current", jsoTelemetry, firebaseData);
				res = SendToFirebase(timestamp, "telemetry_current/timestamp", jsoTelemetry, firebaseData);
				res = SendToFirebase(push, "telemetry", jsoTelemetry, firebaseData);
				res = SendToFirebase(appendtimestamp, "", jsoTelemetry, firebaseData);
			}
		#endif
		LogLine(5, __FUNCTION__, "done");

}
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
void loop() {
	String rm;

	#ifdef USE_FIREBASE
		GetSettingsFromFirebase_(firstRun);
		firstRun = false;
		InitFirebaseLogging(firebaseData, FB_BasePath, "log", JSON_BUFFER_LENGTH);

		while (PersistentMemory.GetRunOTA()) {
			LogLine(0, __FUNCTION__, "Starting OTA update. set OTA flag back to false manually");
			ArduinoOTA.handle();
			LogLine(0, __FUNCTION__, "after OTA handling. Checking firebase.");
			GetSettingsFromFirebase_(firstRun);
		}
	#endif

	rm = PersistentMemory.GetrunMode();
	LogLinef(4, __FUNCTION__, "runmode = %s", rm.c_str());
	if (rm.equals(RUNMODE_SOIL) || rm.equals(RUNMODE_WATER) ) {
		if (WaterIfNeeded()) {
			// use deep sleep if it's enabled and we want to soak for a longer period of time
			if ((waterValveA.soakSeconds <= DEEP_SLEEP_SOAK_THRESHOLD) || (!PersistentMemory.GetdeepSleepEnabled())) {
				waterValveA.WaitToSoak();
			}
			else {
				DeepSleepHandler.GotoSleepAndWakeAfterDelay(waterValveA.soakSeconds);
			}
		}
		if (loopCount++ >= NBR_OF_LOOPS_BEFORE_SLEEP) {
			DeepSleepHandler.GotoSleepAndWakeAfterDelay(PersistentMemory.GettotalSecondsToSleep());
		}
	}
	else if (rm.equals(RUNMODE_DISTANCE)) {
		sensorA.ReadSensor();
		UploadTelemetry_();
	}
	else if (rm.equals(RUNMODE_SENSORTEST)) {
		LogLine(4, __FUNCTION__, "Test sensor input");
//		waterValveA.OpenValve();
		sensorA.TestSensor();
//		sensorA.GetDistanceCentimeter();
//		delayNonBlocking(1000);
//		waterValveA.CloseValve();
		UploadTelemetry_();
	}
	else if (rm.equals(RUNMODE_BATTERYTEST)) {
		externalVoltMeter.TestSensor();
		UploadTelemetry_();
	}
	else if (rm.equals(RUNMODE_HARDWARETEST)) {
		testHardware();
	}
#ifdef USE_GAS_SENSOR
	else if (rm.equals(RUNMODE_GAS)) {
		if (!PersistentMemory.GetdeepSleepEnabled()) {
			UploadTelemetry_();
		}
		else {
			DeepSleepHandler.GotoSleepAndWakeAfterDelay(waterValveA.soakSeconds);
		}
		if (loopCount++ >= NBR_OF_LOOPS_BEFORE_SLEEP) {
			DeepSleepHandler.GotoSleepAndWakeAfterDelay(PersistentMemory.GettotalSecondsToSleep());
		}
	}
#endif
#ifdef USE_DHT11_SENSOR
	else if (rm.equals(RUNMODE_DHT11)) {
		UploadTelemetry_();
		LogLine(5, __FUNCTION__, "Uploaded DHT data");
		if (PersistentMemory.GetdeepSleepEnabled()) {
			//			if (loopCount++ >= NBR_OF_LOOPS_BEFORE_SLEEP) {
			LogLine(5, __FUNCTION__, "Call GotoSleep");
			DeepSleepHandler.GotoSleepAndWakeAfterDelay(PersistentMemory.GettotalSecondsToSleep());
			//			}
		}
	}
#endif
	else {
		LogLinef(0, __FUNCTION__, "Illegal option chosen: %s . Resetting runMode to normal", rm.c_str());
		PersistentMemory.SetrunMode(DefaultRunmode);
		LED_Flashes(200, 100);
	}

#ifdef RUN_ONCE
	while (true) {
		LogLine(1, __FUNCTION__, "wait forever (controlled by RUN_ONCE directive)");
		delayNonBlocking(60000);
	}
#else
	int d = PersistentMemory.GetmainLoopDelay();
	LogLinef(3, __FUNCTION__, "waiting mainLoopDelay: %d", d);
	delayNonBlocking(d * 1000);
#endif
}


void TestLoop(String logStr, int LEDflash, int LEDblinkdelay) {
	LogLine(3, __FUNCTION__, logStr.c_str());
	LED_Flashes(LEDflash, LEDblinkdelay);
}

#ifdef MEASURE_INTERNAL_VCC
	ADC_MODE(ADC_VCC); //vcc read
	float GetInternalVcc() {
		//at the beginning of sketch
		return (ESP.getVcc() / 1000.0);
	}
#endif

void InitUnitTest() {
	delayNonBlocking(500);
	Serial.begin(115200);

	InitDebugLevel(4);
	PersistentMemory.SetdebugLevel(4);

	// read persistent memory
	PersistentMemory.init(false, 20, "PCB v5.2 - #1", 0, 0, 10, 4);   // false: read from memory.  true: initialize
	SetFBDebugLevel(PersistentMemory.GetdebugLevel());
	LogLine(1, __FUNCTION__, "BEGIN");
	LogLinef(2, __FUNCTION__, "Sleep cycle %d of %d", PersistentMemory.ps.currentSleepCycle, PersistentMemory.ps.maxSleepCycles);

	// check for crazy values
	if (PersistentMemory.ps.currentSleepCycle >= 12 || PersistentMemory.ps.maxSleepCycles >= 12) {
		LogLine(2, __FUNCTION__, "Resetting counters");
		PersistentMemory.SetmaxSleepCycles(0);
		PersistentMemory.SetvalveOpenDuration(0);
		PersistentMemory.ps.currentSleepCycle = 0;
	}

#ifdef USE_WIFI 
	ConnectToWifi();
	WiFi.macAddress(localmacAddr);
	PersistentMemory.SetmacAddress(localmacAddr);
	Serial.println(PersistentMemory.GetmacAddress());

	// TODO: move time fetching to Wifi_nnr and generalize it.
	configTime(0, 0, "pool.ntp.org", "time.nist.gov");   // note - it may take some HOURS before actual time is correct.
	AdjustTime(2);  // configTime adjustments does not work!! Hence we adjust and include summertime permanently.
	while (time(nullptr) < 1510644967) {
		delayNonBlocking(10);
	}
	if (getCurrentTimeB()) {
		LogLine(5, __FUNCTION__, "Time fetched and adjusted");
	}
	else {
		LogLine(0, __FUNCTION__, "Time NOT fetched and adjusted");
	}
#endif

/*
#ifdef USE_FIREBASE
	FB_BasePath = FB_DEVICE_PATH + PersistentMemory.GetmacAddress();
	Firebase.begin(FIREBASE_HOST, FIREBASE_AUTH);
	//RemoveTelemetryFromFirebase(); UploadLog_("Setup(): ALL TELEMETRY REMOVED");
	UploadStateAndSettings_();
#endif
*/
	if (PersistentMemory.ps.currentSleepCycle != 0) {
		DeepSleepHandler.GoToDeepSleep();
	}
}

void testHardware() {

//	DeepSleepHandler.GotoSleepAndWakeUpAtTime(PersistentMemory.GetWakeTime());
	
	TestLoop("testHardware: begin", 1, 500);

	AnalogMux.OpenChannel(0);
	TestLoop("testHardware: open OpenChannel", 1, 3000);

	AnalogMux.CloseMUXpwr();
	TestLoop("testHardware: CloseMUXpwr", 1, 3000);

	float f = externalVoltMeter.ReadVoltage();
	TestLoop("testHardware: ReadVoltage", 1, 3000);

	boolean b = soilHumiditySensorA.CheckIfWater();
	TestLoop("testHardware: CheckIfWater", 1, 3000);

	waterValveA.OpenValve();
	TestLoop("testHardware: OpenValve", 1, 1000);

	waterValveA.CloseValve();
	TestLoop("testHardware: CloseValve", 1, 3000);

	LED_Flashes(500, 100);
	
}

void SOFT_RESET_ARDUINO() {
	LogLine(0, __FUNCTION__, "\n**************************************************\n**************************************************\n\nRESETTING ARDUINO WHEN BLINKING IS DONE\n\n**************************************************\n**************************************************\n");
	for (int m = 30; m>0; m--) {
		//log		LogLine(0, __FUNCTION__, String(m) + " minutes to reset");
		for (int s = 0; s < 60; s++) {
			digitalWrite(LED_BUILTIN, HIGH);
			delayNonBlocking(500);
			digitalWrite(LED_BUILTIN, LOW);
			delayNonBlocking(500);
		}
	}
	LogLine(0, __FUNCTION__, "GO RESET");
	ESP.restart();
}

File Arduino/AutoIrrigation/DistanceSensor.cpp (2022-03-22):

#include "DistanceSensor.h"
#include "AnalogMux.h"

void DistanceSensorClass::init(int _pinNbr, char _name[], int _muxChannel, SensorHandlerClass::SensorType _sensorType, int _distLimit)
{
	strcpy(name, _name);
	pinNbr = _pinNbr;
	muxChannel = _muxChannel;
	sensorType = _sensorType;
	lastAnalogueReadingDist = 0.0;
	distLimitCentimeter = _distLimit;

	pinMode(pinNbr, INPUT);
	L::LogLinef(2, __FUNCTION__, "MUX channel:%d   analog pin:%d   name:%s   _distLimit=%d    _sensorType=%d", muxChannel, pinNbr, name, _distLimit, this->sensorType);
}

void DistanceSensorClass::AddTelemetryJson(FirebaseJson* json) {
	//this->soilTm.distCm = (double)this->GetDistanceCentimeter()/1024.0*100;
	this->soilTm.distCm = (double)this->lastAnalogueReadingDist / 1024.0 * 100.0;
	json->add("Hum", this->soilTm.distCm);
}

void DistanceSensorClass::SetdistLimitPct(int _distLimitCentimeter) {
	this->distLimitCentimeter = _distLimitCentimeter;
}

float DistanceSensorClass::ReadSensor() {
	float raw = 0.0;
	float res = 0;
	int AVG_COUNT;
	if (sensorType == SensorHandlerClass::DistanceSensor) {
		AVG_COUNT = 5;
	}
	else {
		AVG_COUNT = 3;
	}

	L::LogLinef(3, __FUNCTION__, "READING DISTANCE FROM analog MUX channel %d pin %d", muxChannel, this->pinNbr);
	AnalogMux.OpenChannel(muxChannel);
	delayNonBlocking(100);
	for (int i = 0; i < AVG_COUNT; i++) {
		delayNonBlocking(50);
		raw = analogRead(this->pinNbr);
		L::LogLinef(5, __FUNCTION__, "Value: %f", raw);
		res += raw;
	}
	//	delayNonBlocking(100);
	AnalogMux.CloseMUXpwr();
	res /= AVG_COUNT;
	this->lastAnalogueReadingDist = res;

	L::LogLinef(2, __FUNCTION__, "Distance raw value: %f", res);
	return res;
}

float DistanceSensorClass::GetDistanceCentimeter() {

	float adjFactor = 1.8;   // rough measure
	float cm = 0;
	switch (this->sensorType) {
		case SensorHandlerClass::DistanceSensor:
			L::LogLinef(5, __FUNCTION__, "lastAnalogueReadingDist Value: %f", this->lastAnalogueReadingDist);
/*			cm = adjFactor * pow(3027.4 / this->lastAnalogueReadingDist, 1.2134); //convert readings to distance(cm)
			if (cm < 10) { cm = 10; }
			if (cm > 120) { cm = 120; }
*/
			cm = this->lastAnalogueReadingDist;
			break;
		default:
			L::LogLine(1, __FUNCTION__, "unexpected sensor type");
			break;
	}

	L::LogLinef(3, __FUNCTION__, "  raw=%f  cm=%f", this->lastAnalogueReadingDist, cm);
	return cm;
}

boolean DistanceSensorClass::CheckIfWater() {
	float res = 0;
	boolean val;

	val = DRY;
	if (!SIMULATE_SENSORS) {
		res = this->ReadSensor();
		this->lastAnalogueReadingDist = res;
		if (GetDistanceCentimeter() <= this->distLimitCentimeter) {   // the greater distance, the less water
			L::LogLine(3, __FUNCTION__, "  Soil or reservoir is WET");
			val = WET;
		}
		else {
			L::LogLine(3, __FUNCTION__, "  Soil or reservoir is DRY");
			val = DRY;
		}
	}
	return val;
}

float DistanceSensorClass::GetlastAnalogueReadingDist() {
	return this->lastAnalogueReadingDist;
}

float DistanceSensorClass::TestSensor() {
	
	float raw = 0.0;
	float res = 0;
	int AVG_COUNT;
	if (sensorType == SensorHandlerClass::DistanceSensor) {
		AVG_COUNT = 5;
	}
	else {
		AVG_COUNT = 3;
	}

	L::LogLinef(3, __FUNCTION__, "READING DISTANCE FROM analog MUX channel %d pin %d", muxChannel, this->pinNbr);
	AnalogMux.OpenChannel(muxChannel);
	delayNonBlocking(100);
	for (int i = 0; i < AVG_COUNT; i++) {
		delayNonBlocking(50);
		raw = analogRead(this->pinNbr);
		L::LogLinef(5, __FUNCTION__, "Value: %f", raw);
		res += raw;
	}
//	delayNonBlocking(100);
	AnalogMux.CloseMUXpwr();
	res /= AVG_COUNT;
	this->lastAnalogueReadingDist = res;
	L::LogLinef(1, __FUNCTION__, "Raw average Value: %f", res);
	return res;

}




DistanceSensorClass DistanceSensor;

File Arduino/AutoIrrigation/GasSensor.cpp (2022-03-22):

// This "sensor" is special, because it's located at another device (co_monitor).
// What this file does is establish serial comm to that device.
// 

#include "GasSensor.h"
#include "serialPortHandler.h"


void GasSensorClass::init(int _pinNbr, char _name[], int _muxChannel, SensorHandlerClass::SensorType _sensorType)
{
	// For serial comm to other Arduino:
	SetupSerialPort();

	strcpy(name, _name);
	pinNbr = _pinNbr;
	muxChannel = _muxChannel;
	sensorType = _sensorType;
	lastAnalogueReading = 0.0;

	pinMode(pinNbr, INPUT);
	//log	L::LogLine(2, __FUNCTION__, "MUX channel:" + String(muxChannel) + " analog pin:" + String(pinNbr) + " name:" + String(name));
}

const int jsonMaxSize = 500;
char jsonStr[jsonMaxSize];

boolean GasSensorClass::GetTelemetryJson(FirebaseJson *json) {
	FirebaseJsonData jsonData;

	L::LogLine(4, __FUNCTION__, "begin");
	if (ReadSerialJsonOnce(jsonStr, jsonMaxSize)) {
		L::LogLine(4, __FUNCTION__, "fetched from serial port");
		L::LogLine(4, __FUNCTION__, jsonStr);

		//	Serial.println(jsonStr);
		json->setJsonData(jsonStr);

		// assign internal variables
		json->get(jsonData, "cur_ppm");		this->gasTm.cur_CO_ppm_measurement = jsonData.doubleValue;
		json->get(jsonData, "last_ppm");	this->gasTm.last_CO_ppm_measurement = jsonData.doubleValue;
		json->get(jsonData, "sens_val");	this->gasTm.sens_val = jsonData.doubleValue;
		json->get(jsonData, "phase");		this->gasTm.phase = jsonData.intValue;
		L::LogLine(4, __FUNCTION__, "finished");
		return true;
	}
	L::LogLine(2, __FUNCTION__, "no telemetry received from device via serial port");
	return false;
}

float GasSensorClass::ConvertToPPM(float rawVal) {

	float RS_gas = 0;
	float ratio = 0;
	float sensorVolt = 0;
	float sensorVolt_5Vnorm = 0;
	float R0 = 340000;
	float MIN_V = 0.08;
	float MAX_V = 0.4;

	sensorVolt = (rawVal / 1024);
	sensorVolt_5Vnorm = (sensorVolt - MIN_V) * 5.0 / (MAX_V - MIN_V);
	RS_gas = (5.0 - sensorVolt_5Vnorm) / sensorVolt_5Vnorm;

	ratio = RS_gas / R0; //Replace R0 with the value found using the sketch above
	float x = 1538.46 * ratio;
	float ppm = pow(x, -1.709);
	Serial.printf("\nPPM: %f  RAW:%f  sensorVolt=%f  sensorVolt_5Vnorm=%f", ppm, rawVal, sensorVolt, sensorVolt_5Vnorm);
	return ppm;
}

float GasSensorClass::GetlastPPM() {
	return this->lastPPM;
}

float GasSensorClass::TestSensor() {
	float raw=0;
	for (int i = 0; i < 1; i++) {
		//this->ReadSerialJsonOnce();
		this->lastAnalogueReading = raw;
	}
	return raw;
}

/*
float ReadSensorNotUsed() {
	int raw = 0;
	float res = 0;
	int AVG_COUNT = 60;
	float ppm = 0;

	//log	L::LogLine(4, __FUNCTION__, "READING GAS LEVEL FROM analog MUX channel " + String(muxChannel));
	delayNonBlocking(10);  // allow voltage to settle after valve open
	AnalogMux.OpenChannel(muxChannel);
	for (int i = 0; i < AVG_COUNT; i++) {
		delayNonBlocking(1000);
		raw = analogRead(pinNbr);
		res += raw;
		//log 		L::LogLine(4, __FUNCTION__, "Raw Value: " + String(raw) );
	}
	AnalogMux.CloseMUXpwr();
	res /= AVG_COUNT;
	this->lastPPM = ConvertToPPM(res);
	//log L::LogLine(1, __FUNCTION__, "Raw Value: " + String(res) + "  =  " + this->lastPPM + " ppm" );
	return res;
}

*/

GasSensorClass GasSensor;

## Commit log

2019-03-21 Arduino side: - Firebase interface including: -- read/write of state for configuring during runtime -- write telemetry -- log -- Device creation - Deep Sleep configurable from Firebase / app - Abilit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
    Android Side
    - Read / write to Firebase
    - Support for multiple devices
    - Graph (timeline)
    - Still missing:
    -- Some actions on added data (changes works fine). Basics works fine.
    -- Better scrolling in graphs
    -- more screens (e.g. multi-device view)
    [AutoIrrigation.ino, DeviceActivity.java]
2019-03-21 Added Wiring diagram, layout for wrapping and documentation
    [Base floor.stl, Solar Opladere.xlsx, autonomous watering unit - PRINTBOARD v1.sch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]
2019-04-04 - Changed DeepSleep handling. - Modified Firebase parameters handling Deep Sleep - Added time adjustment to danish summertime (permanently). - Added power down of sensor unit during setup() - Changed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
    [Solar Opladere.xlsx, irrigation_5Vvalve_4N25.sch, irrigation_5Vvalve_4N25_WRAP.kicad_pcb]
2019-04-04 Adding files for 3D printing and schematics + PCB/wrap layout
    [Corner fixtures for PCBs.stl, Irrigation unit - 5V mini valve v1.f3d, Irrigation unit - PCB board v2.f3d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]
2019-04-04 Updated JSON database layout in Firebase, Arduino and Android. Documented in Word file.
    [Bottom box.stl]
2019-04-20 Works before Google Firebase interface has been changed (by Google)
    [Irrigation unit - Main box v29.stl, Irrigation unit on PCB onboard 18650 v22.iges, Irrigation unit on PCB onboard 18650 v22.stl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]
2019-04-23 Change averaging period for battery voltage (from 10 samples to 3)
2019-04-30 Box for external valve
    [Valve unit v4.stl, irrigation_5Vvalve_4N25_18650_WRAP.kicad_pcb]
2019-06-21 Sleep until scheduled time of day. Some started work on gas sensor (not finished)
2019-07-28 LogLinef changed to follow syntak in sprintf(). Logline and Loglinef now taking only char[] as input (i.e. no longer using String). LogLineFB and LogLinefFB introduced to enable logging to Firebase c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
    [AnalogMux.cpp, AutoIrrigation.ino, GasSensor.cpp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]
2019-08-24 Compiles and runs without crashes: - logging to cloud - 4 waketimes (included, but not in use)
    [AutoIrrigation.ino, globals.h]
2019-09-03 - Unit test of DeepSleepHandler - Corrected some errors. - DeepSleepHandler now works
    [AutoIrrigation.ino]
2019-09-15 Small correction in deep sleep: wait for final sleep loop before measuring
    [AutoIrrigation.ino]
2019-09-20 Fixed: Multiple Vcc lines on graph in app.
    [DeviceActivity.java]
2019-11-13 PCB changes: - Simplified power supply (removing Step-up, including step-down)
    [irrigation v5.2.sch, irrigation v6.0.kicad_pcb, irrigation v6.0.sch]
2019-11-13 Created zip file for new PCB (v6.0)
2019-11-13 PCB version 6.0 ZIP containing the correct version (in case of doubt)
    [irrigation v5.2.sch, irrigation v6.0.kicad_pcb, irrigation v6.0.sch]
2019-12-08 Updating documentation Working on PCB board version 6.0 (only 5V and different power supply circuit)
    [Corner fixtures for PCBs.stl, irrigation v5.2.sch, irrigation v6.0.kicad_pcb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]
2019-12-15 Clean-up for making public
    [Base floor.stl, Bottom box.stl, Irrigation unit - 5V mini valve v1.f3d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]
2019-12-15 Initial public version.
    [Irrigation unit - Main box v29.stl, Solar Chargers.xlsx, Solar Opladere.xlsx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]
2020-01-01 temporary work - not working
    [AutoIrrigation.ino, GasSensor.cpp]
2020-01-12 Upgraded to latest version (2.7.6) of Firebase-ESP8266 by @Mobitz. Now support for many types of telemetry; defined by the sensors attached (they now produce their own telemetry which is collected by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
    [AutoIrrigation.ino, GasSensor.cpp, SoilHumiditySensor.cpp]
2020-01-18 Gas sensor now working on D1 side: - receive JSON via serial port from external sensing device - build telemetry and send it.
2020-02-01 Update of Android app to include a gas sensor device.
2020-03-28 Added ventilation holes in case
    [Irrigation unit - Main box (side mounted) v21.stl]
2020-03-28 Bugfix: totslp forgotten in settings in Firebase Changed to soil sensor mode.
    [AutoIrrigation.ino]
2020-03-29 Added "soil" as default value for device type Changed debug levels generally.
2020-10-25 Included DHT11 temperature + humidity sensor
2020-10-25 Reorganized compile flags and checked that Irrigation device was still working.
2020-11-02 New 3D files for a small sensor (DHT22) Added a compile_flag header file
    [Simple sensor - bottom v2.stl, Simple sensor - bottom v4.stl, Simple sensor - top v2.stl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]
2021-02-09 Bug fix + preparation for OTA update: - replace delay with non-blocking delay
    [AnalogMux.cpp, GasSensor.cpp, SoilHumiditySensor.cpp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]
2021-02-09 Autodetect between DHT11 and DHT22 (not sure the library function is working though). Now defaults to DHT22. For DHT22: handling negative temperatures.
2021-02-09 - Cleanup - removed code referring to Google Cloud (not Firebase)
    - Updates to Firebase interface + upgrade og API:
    - Made library for (almost) all direct communication to Firebase
    - Simplified control structure in AutoIrrigation.ino
    - Error fix:
    - Updates to LogLib to handle error when sending "/" or "\" to Firebase log
    - Prepare for OTA update (not fully functional yet):
    - control OTA from Firebase setting "OTA"
    - update persistent memory structure to include setting
    - update control structures to include OTA handling. (Not yet working)
    [AutoIrrigation.ino, TestOTAupdate.ino, compile_flags.h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]
2021-03-17 Device: - re-adding humidity to sensors (was removed and zeroed)
    App:
    - swapped Humidity ad Wifi between primary and secondary axis for temperature sensors.
    - No display of Wifi anymore for temperature sensors
    [AutoIrrigation.ino]
2021-05-13 small test of an infrared water sensor
2021-10-18 Initial distance sensor. Not finished.
2022-01-02 Use of new version of PersistentMemory to improve Firebase integration. Using v6 (instead of v5) of ArduinoJson library
2022-01-02 Added exception handler for error with inserted timestamp in telemetry.
2022-01-18 LEDHandler => NNR_LEDHandler
2022-03-22 Android App: Dynamic device display. (feb 2022)
    Made on wrong code folder on summer house PC
2022-04-10 Support for wew device type: Pump controller
2022-12-27 Move Firebase base path to v2. New feature: purge every N'th sample New feature: add offset to data
